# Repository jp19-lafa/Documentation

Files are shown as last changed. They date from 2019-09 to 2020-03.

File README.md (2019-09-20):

[][contributors-url]
[][forks-url]
[][stars-url]
[][issues-url]
[][license-url]

<!-- PROJECT LOGO -->
<br />
<p align="center">
  <a href="https://github.com/jp19-lafa/Documentation">
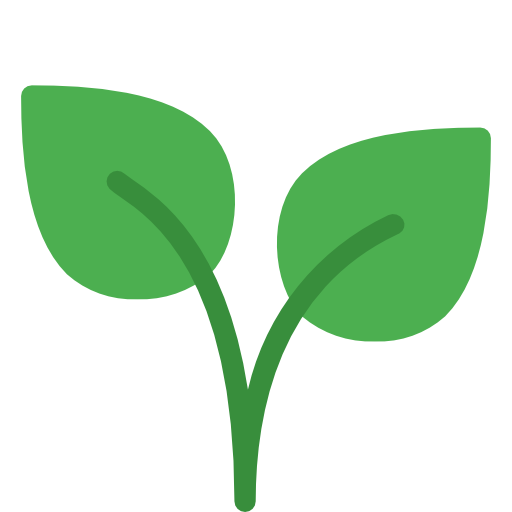
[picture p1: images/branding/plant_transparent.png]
    
  </a>

  <h3 align="center">DOCUMENTATION</h3>

  <p align="center">
    Wiki for farmlab
    <br />
    <a href="https://github.com/jp19-lafa/Documentation/wiki"><strong>Explore the docs »</strong></a>
    <br />
    <br />
    <a href="https://github.com/jp19-lafa/Documentation/issues">Report Bug</a>
    ·
    <a href="https://github.com/jp19-lafa/Documentation/issues">Request Feature</a>
  </p>
</p>

<!-- TABLE OF CONTENTS -->
## Table of Contents

* [Table of Contents](#table-of-contents)
* [About The Project](#about-the-project)
* [Roadmap](#roadmap)
* [Contributing](#contributing)
* [License](#license)
* [Team](#team)

<!-- ABOUT THE PROJECT -->
## About The Project
FarmLab is a class project for Smart Systems & IoT 2019 @ AP Antwerp. FarmLab is an automated hydroponics farm that utilizes an array of sensor to make smart decisions an create the optimal growing environment. Multiple nodes can work together to create a big farm network.

The cultivation of these plants follow the 'hydroponics' technique. This means the plants are planted directly in water without any type of soil. They are fed by nutrients added to that water.

_For the full explination please refer to the [Wiki](https://github.com/jp19-lafa/Documentation/wiki)_

<!-- ROADMAP -->
## Roadmap

See the [open issues](https://github.com/jp19-lafa/Documentation/issues) for a list of proposed features (and known issues).

<!-- CONTRIBUTING -->
## Contributing

Contributions are what make the open source community such an amazing place to be learn, inspire, and create. Any contributions you make are **greatly appreciated**.

1. Fork the Project
2. Create your Feature Branch (`git checkout -b feature/AmazingFeature`)
3. Commit your Changes (`git commit -m 'Add some AmazingFeature'`)
4. Push to the Branch (`git push origin feature/AmazingFeature`)
5. Open a Pull Request

<!-- LICENSE -->
## License

Distributed under the MIT License. See `LICENSE` for more information.

<!-- Team -->
## Team

Meurs Michiel - michiel.meurs1@gmail.com
<br>
Meyers Tom - tom@odex.be
<br>
Van Hoof Jonas - Jonas.vanhoof@student.ap.be
<br>
Vinck Ben - <!-- TODO: add a e-mail of Vincks choosing-->
<br>
Willemsen Matthias - <!-- TODO: add a e-mail of Willemsen's choosing-->

Project Link: [https://github.com/jp19-lafa/Documentation](https://github.com/jp19-lafa/Documentation)

<!-- MARKDOWN LINKS & IMAGES -->
<!-- https://www.markdownguide.org/basic-syntax/#reference-style-links -->
[contributors-shield]: https://img.shields.io/github/contributors/jp19-lafa/Documentation.svg?style=flat-square
[contributors-url]: https://github.com/jp19-lafa/Documentation/graphs/contributors
[forks-shield]: https://img.shields.io/github/forks/jp19-lafa/Documentation.svg?style=flat-square
[forks-url]: https://github.com/jp19-lafa/Documentation/network/members
[stars-shield]: https://img.shields.io/github/stars/jp19-lafa/Documentation.svg?style=flat-square
[stars-url]: https://github.com/jp19-lafa/Documentation/stargazers
[issues-shield]: https://img.shields.io/github/issues/jp19-lafa/Documentation.svg?style=flat-square
[issues-url]: https://github.com/jp19-lafa/Documentation/issues
[license-shield]: https://img.shields.io/github/license/jp19-lafa/Documentation.svg?style=flat-square
[license-url]: https://github.com/jp19-lafa/Documentation/blob/master/LICENSE.txt
[product-screenshot]: https://raw.githubusercontent.com/jp19-lafa/Documentation/master/images/branding/plant_transparent.svg

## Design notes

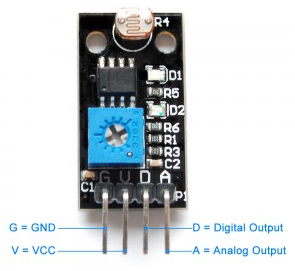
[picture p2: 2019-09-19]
images/sensors/Pinout_LightSensor.png

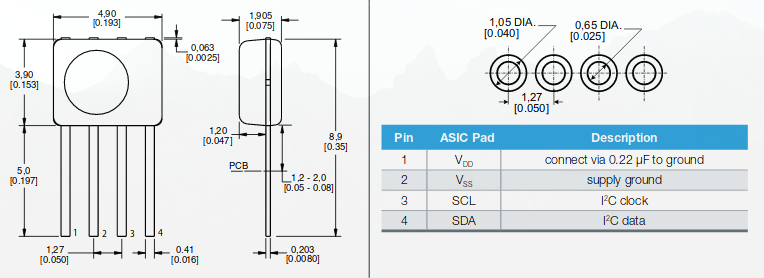
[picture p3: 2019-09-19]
images/sensors/Pinout_HIH6030.png

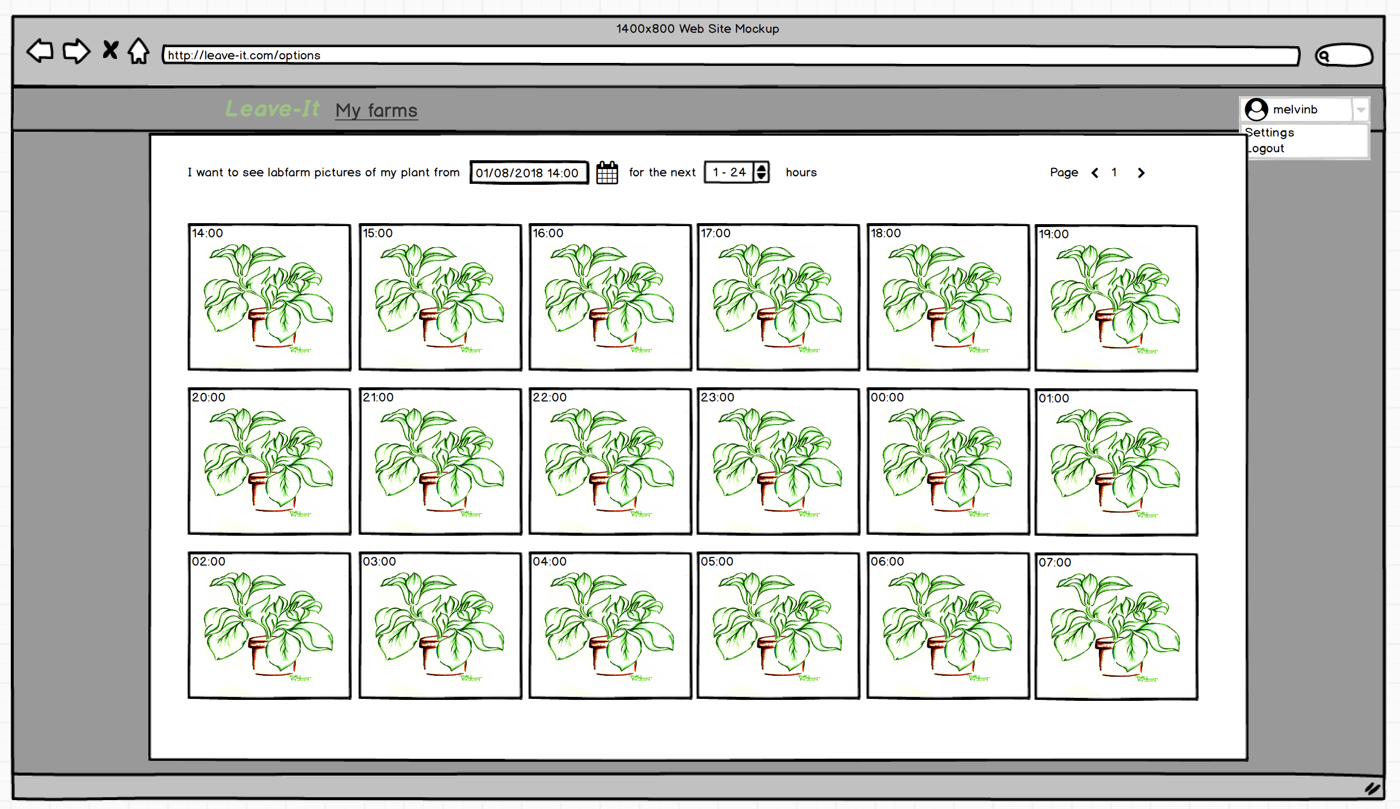
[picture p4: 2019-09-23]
images/web/labfarm_picture_overview_mockup.png

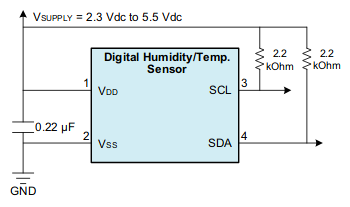
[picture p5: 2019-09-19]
images/sensors/Schematic_HIHI6030.png

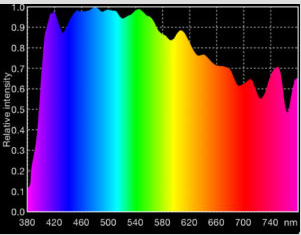
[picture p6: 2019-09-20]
images/actuators/Light_spectrum.png

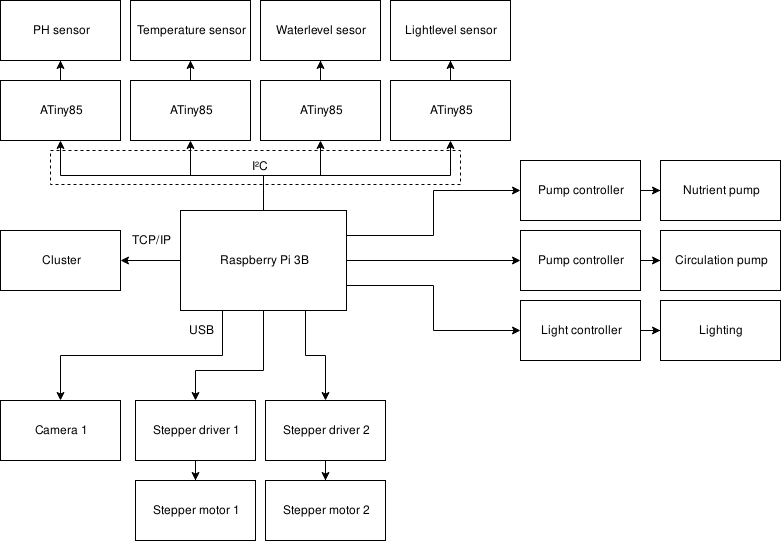
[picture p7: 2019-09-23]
images/general/hardware_blockdiagram.png

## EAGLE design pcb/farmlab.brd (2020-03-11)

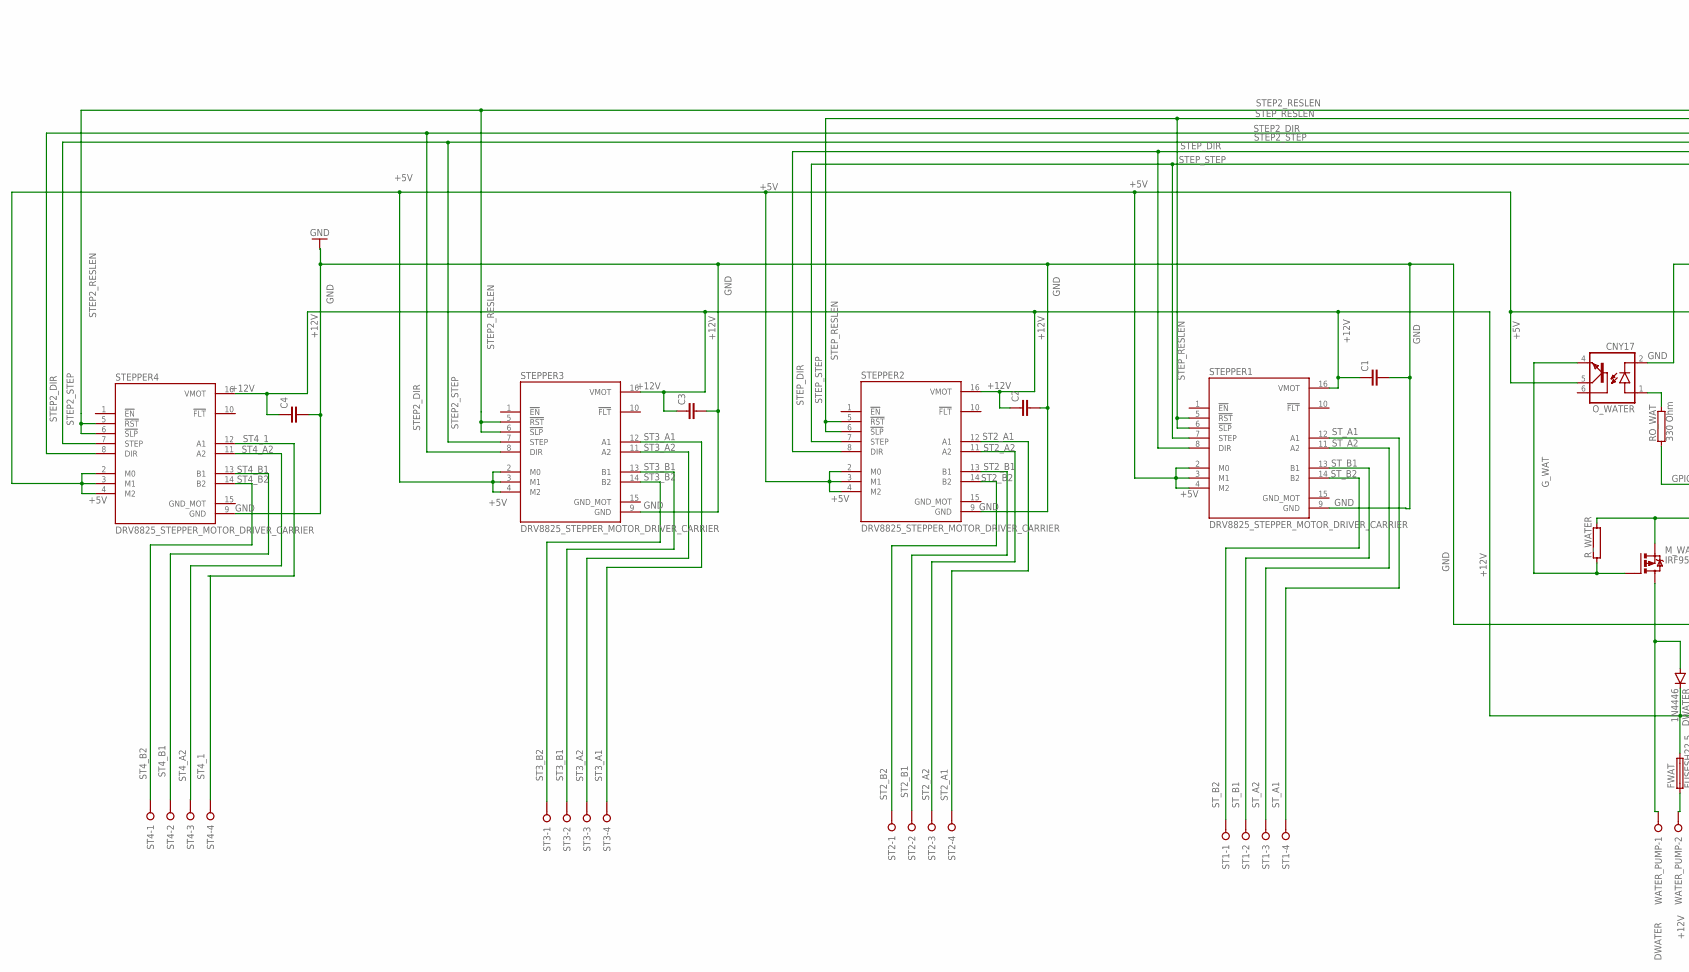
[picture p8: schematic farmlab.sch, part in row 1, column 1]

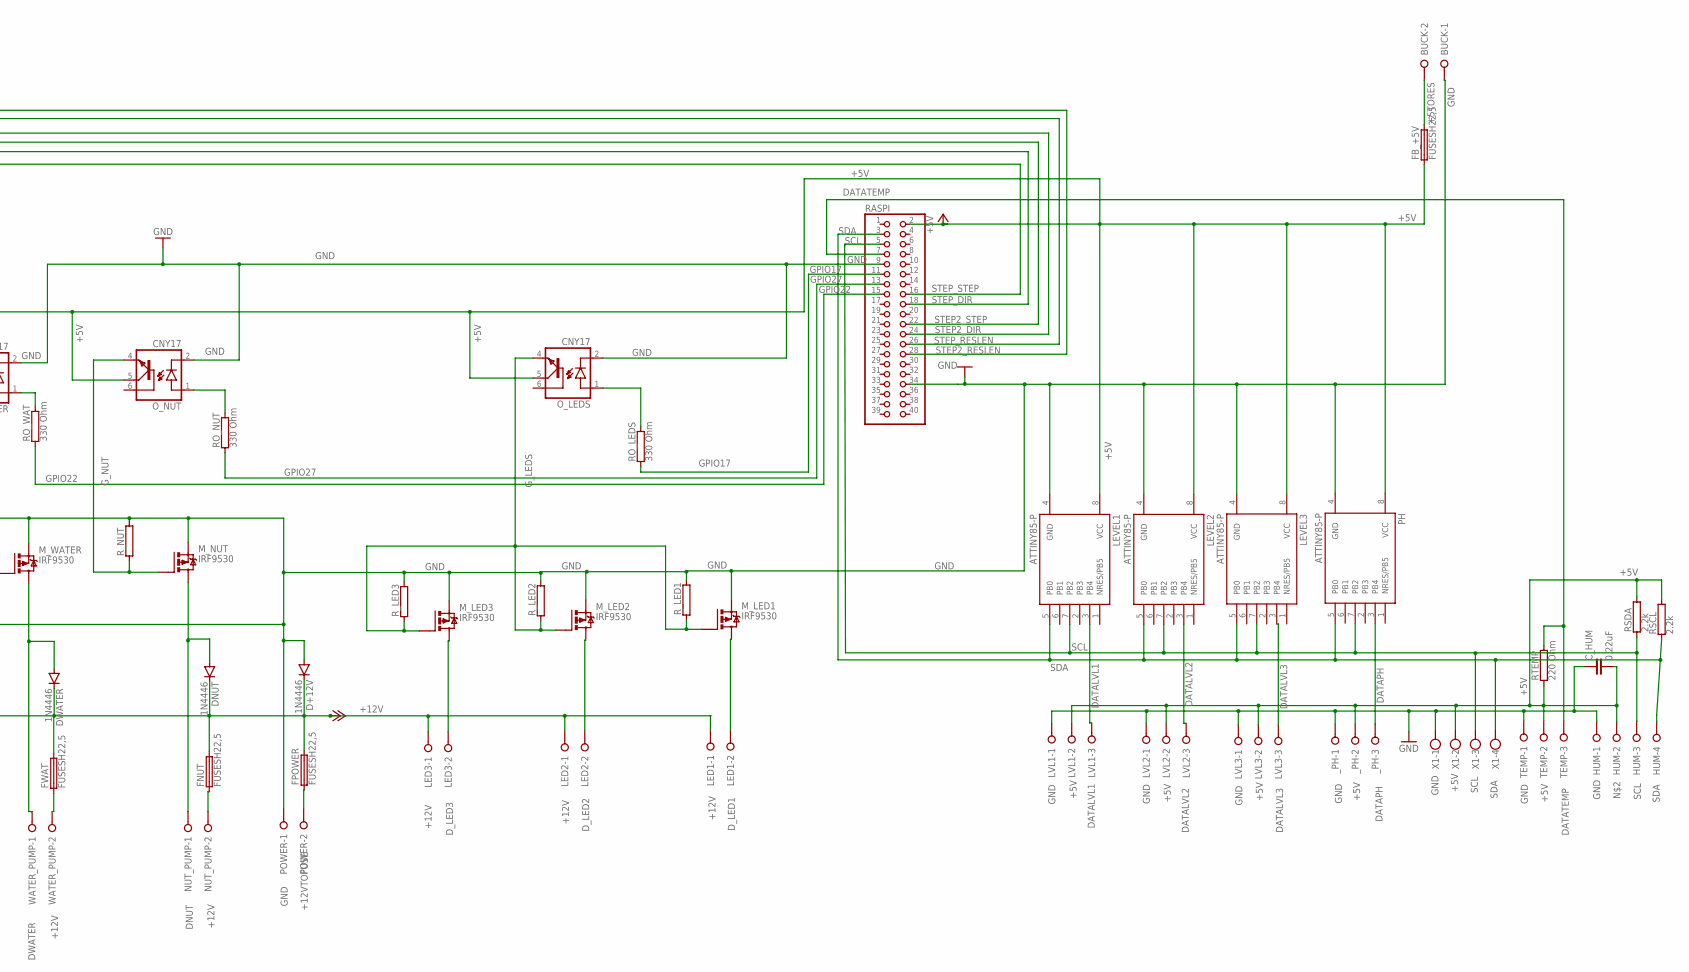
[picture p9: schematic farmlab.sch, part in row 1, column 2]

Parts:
BUCK: W237-02P; W237-132
C1, C2, C3, C4: C2.5/6; C2.5-6
C_HUM: 0.22uF; C2.5-6
D+12V: 1N4446; DO35-10
DNUT: 1N4446; DO35-10
DWATER: 1N4446; DO35-10
FB_+5V: FUSESH22,5; SH22,5
FNUT: FUSESH22,5; SH22,5
FPOWER: FUSESH22,5; SH22,5
FWAT: FUSESH22,5; SH22,5
HUM: W237-04P; W237-4P
LED1, LED2, LED3: W237-02P; W237-132
LEVEL1, LEVEL2, LEVEL3: ATTINY85-P; PDIP08_300MIL
LVL1, LVL2, LVL3: W237-3E
M_LED1, M_LED2, M_LED3: IRF9530; TO220BV
M_NUT: IRF9530; TO220BV
M_WATER: IRF9530; TO220BV
NUT_PUMP: W237-02P; W237-132
O_LEDS: CNY17; DIL06
O_NUT: CNY17; DIL06
O_WATER: CNY17; DIL06
PH: ATTINY85-P; PDIP08_300MIL
POWER: W237-02P; W237-132
RASPI: PINHD-2X20; 2X20
RO_LEDS: 330 Ohm; AC03
RO_NUT: 330 Ohm; AC03
RO_WAT: 330 Ohm; AC03
RSCL: 2.2k; AC03
RSDA: 2.2k; AC03
RTEMP: 220 Ohm; AC03
R_LED1, R_LED2, R_LED3: RAC03; AC03
R_NUT: RAC03; AC03
R_WATER: RAC03; AC03
ST1, ST2, ST3, ST4: W237-04P; W237-4P
STEPPER1, STEPPER2, STEPPER3, STEPPER4: DRV8825_STEPPER_MOTOR_DRIVER_CARRIER; IC_DRV8825_STEPPER_MOTOR_DRIVER_CARRIER
TEMP: W237-3E
WATER_PUMP: W237-02P; W237-132
X1: W237-4
_PH: W237-3E

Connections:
+5TORES: BUCK.2, FB_+5V.2
+5V: C_HUM.2, FB_+5V.1, LEVEL1.8 (VCC), LEVEL2.8 (VCC), LEVEL3.8 (VCC), LVL1.2, LVL2.2, LVL3.2, O_LEDS.5 (COL), O_NUT.5 (COL), O_WATER.5 (COL), PH.8 (VCC), RASPI.2, RSCL.2, RSDA.2, RTEMP.1, STEPPER1.2 (M0), STEPPER1.3 (M1), STEPPER1.4 (M2), STEPPER2.2 (M0), STEPPER2.3 (M1), STEPPER2.4 (M2), STEPPER3.2 (M0), STEPPER3.3 (M1), STEPPER3.4 (M2), STEPPER4.2 (M0), STEPPER4.3 (M1), STEPPER4.4 (M2), TEMP.2, X1.2, _PH.2
+12V: C1.1, C2.1, C3.1, C4.1, D+12V.C, DNUT.C, DWATER.C, FNUT.2, FPOWER.2, FWAT.2, LED1.1, LED2.1, LED3.1, STEPPER1.16 (VMOT), STEPPER2.16 (VMOT), STEPPER3.16 (VMOT), STEPPER4.16 (VMOT)
+12VTOFUSE: FPOWER.1, POWER.2
DATALVL1: LEVEL1.3 (PB4), LVL1.3
DATALVL2: LEVEL2.3 (PB4), LVL2.3
DATALVL3: LEVEL3.3 (PB4), LVL3.3
DATAPH: PH.3 (PB4), _PH.3
DATATEMP: RASPI.7, RTEMP.2, TEMP.3
DNUT: DNUT.A, M_NUT.D, NUT_PUMP.1
DWATER: DWATER.A, M_WATER.D, WATER_PUMP.1
D_LED1: LED1.2, M_LED1.D
D_LED2: LED2.2, M_LED2.D
D_LED3: LED3.2, M_LED3.D
GND: BUCK.1, C1.2, C2.2, C3.2, C4.2, C_HUM.1, D+12V.A, HUM.1, LEVEL1.4 (GND), LEVEL2.4 (GND), LEVEL3.4 (GND), LVL1.1, LVL2.1, LVL3.1, M_LED1.S, M_LED2.S, M_LED3.S, M_NUT.S, M_WATER.S, O_LEDS.2 (C), O_NUT.2 (C), O_WATER.2 (C), PH.4 (GND), POWER.1, RASPI.9, RASPI.34, R_LED1.2, R_LED2.2, R_LED3.2, R_NUT.2, R_WATER.2, STEPPER1.9 (GND), STEPPER2.9 (GND), STEPPER3.9 (GND), STEPPER4.9 (GND), TEMP.1, X1.1, _PH.1
GND_MOT: STEPPER1.15 (GND_MOT), STEPPER2.15 (GND_MOT), STEPPER3.15 (GND_MOT), STEPPER4.15 (GND_MOT)
GPIO17: RASPI.11, RO_LEDS.1
GPIO22: RASPI.15, RO_WAT.1
GPIO27: RASPI.13, RO_NUT.1
G_LEDS: M_LED1.G, M_LED2.G, M_LED3.G, O_LEDS.4 (EMI), R_LED1.1, R_LED2.1, R_LED3.1
G_NUT: M_NUT.G, O_NUT.4 (EMI), R_NUT.1
G_WAT: M_WATER.G, O_WATER.4 (EMI), R_WATER.1
unnamed: O_WATER.1 (A), RO_WAT.2
unnamed: O_NUT.1 (A), RO_NUT.2
unnamed: O_LEDS.1 (A), RO_LEDS.2
unnamed: FNUT.1, NUT_PUMP.2
unnamed: FWAT.1, WATER_PUMP.2
SCL: HUM.3, LEVEL1.7 (PB2), LEVEL2.7 (PB2), LEVEL3.7 (PB2), PH.7 (PB2), RASPI.5, RSDA.1, X1.3
SDA: HUM.4, LEVEL1.5 (PB0), LEVEL2.5 (PB0), LEVEL3.5 (PB0), PH.5 (PB0), RASPI.3, RSCL.1, X1.4
ST2_A1: ST2.4, STEPPER2.12 (A1)
ST2_A2: ST2.3, STEPPER2.11 (A2)
ST2_B1: ST2.2, STEPPER2.13 (B1)
ST2_B2: ST2.1, STEPPER2.14 (B2)
ST3_A1: ST3.4, STEPPER3.12 (A1)
ST3_A2: ST3.3, STEPPER3.11 (A2)
ST3_B1: ST3.2, STEPPER3.13 (B1)
ST3_B2: ST3.1, STEPPER3.14 (B2)
ST4_1: ST4.4, STEPPER4.12 (A1)
ST4_A2: ST4.3, STEPPER4.11 (A2)
ST4_B1: ST4.2, STEPPER4.13 (B1)
ST4_B2: ST4.1, STEPPER4.14 (B2)
STEP2_DIR: RASPI.24, STEPPER3.8 (DIR), STEPPER4.8 (DIR)
STEP2_RESLEN: RASPI.28, STEPPER3.5 (!RST), STEPPER3.6 (!SLP), STEPPER4.5 (!RST), STEPPER4.6 (!SLP)
STEP2_STEP: RASPI.22, STEPPER3.7 (STEP), STEPPER4.7 (STEP)
STEP_DIR: RASPI.18, STEPPER1.8 (DIR), STEPPER2.8 (DIR)
STEP_RESLEN: RASPI.26, STEPPER1.5 (!RST), STEPPER1.6 (!SLP), STEPPER2.5 (!RST), STEPPER2.6 (!SLP)
STEP_STEP: RASPI.16, STEPPER1.7 (STEP), STEPPER2.7 (STEP)
ST_A1: ST1.4, STEPPER1.12 (A1)
ST_A2: ST1.3, STEPPER1.11 (A2)
ST_B1: ST1.2, STEPPER1.13 (B1)
ST_B2: ST1.1, STEPPER1.14 (B2)

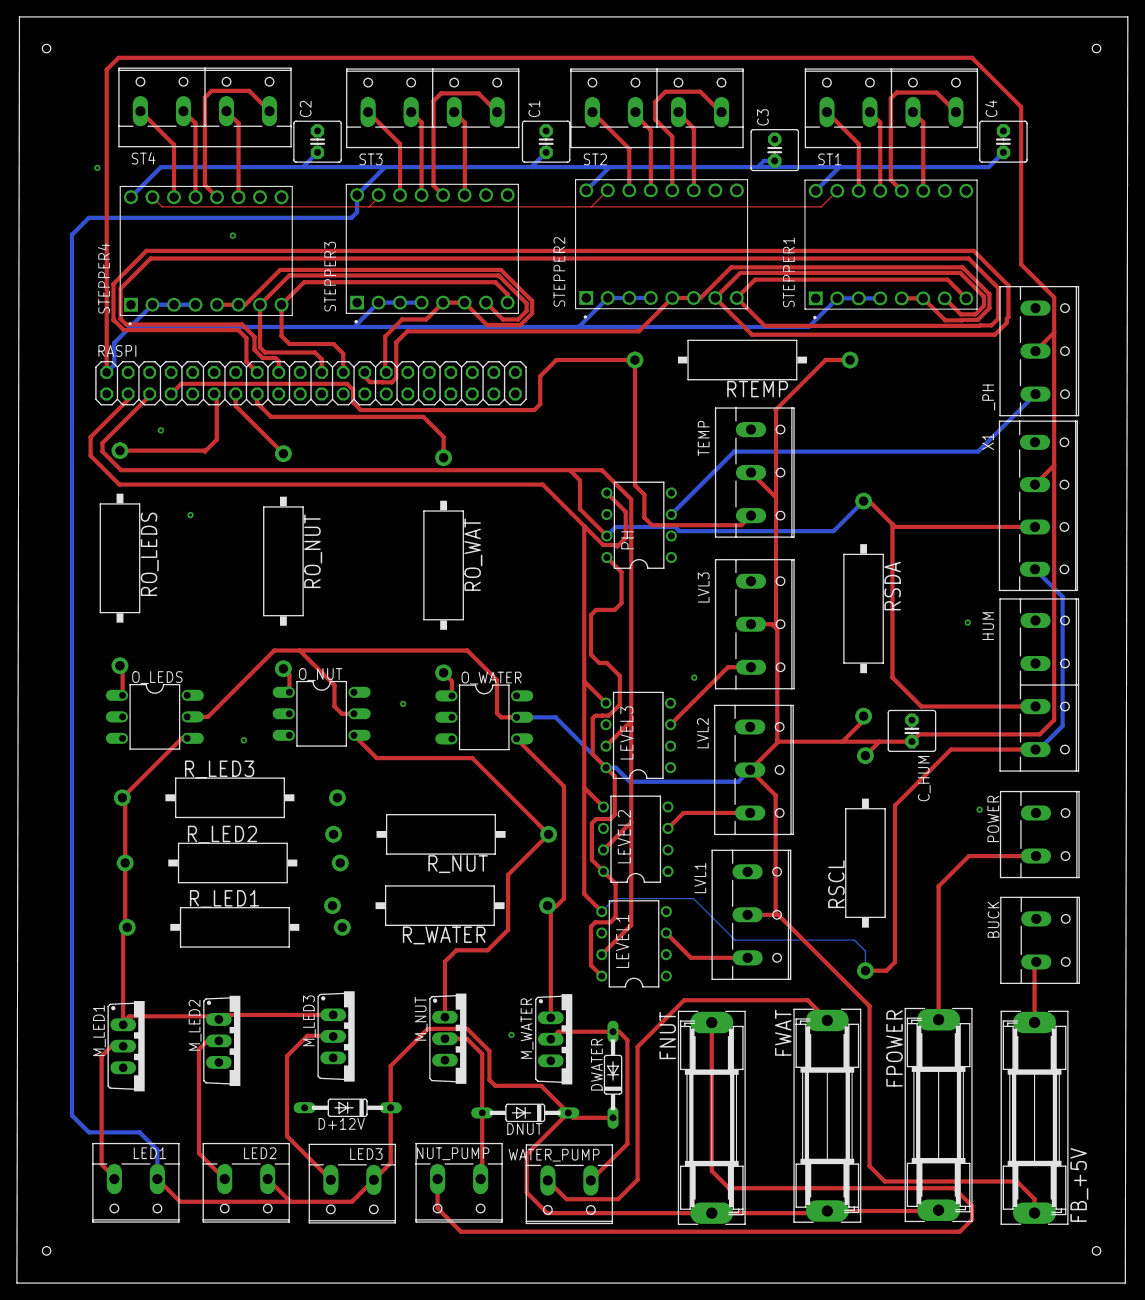
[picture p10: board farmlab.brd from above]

Board: 2 copper layers, 131.2 x 149.5 mm, 58 parts (0 on the bottom side), 51 nets.

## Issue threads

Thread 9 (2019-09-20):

[REFACTOR] readme email list

ShiftyMLG, 2019-09-20:
**Describe the current issue**
E-mails are still missing

**Where is the problem**
What piece of code is a problem
* file: README.md

**How should it change**
Add e-mails

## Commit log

2019-09-16 Added specifications of the sensors + images
2019-09-17 Moved images to Images/Branding All the images that I used in my document Sensors.md where moved to the path Images/Branding.
2019-09-17 Added coding rules to Sensors.md Corrected the style of the document to the coding ruls for a markdown document.
2019-09-19 Moved sensor images Added directory /images/sensors. Moved the sensor images from images/branding to /images/sensors.
2019-09-19 Updated Sensors.md Centered the sensor images and changed the image links. Added the level sensor analysis to the document.
2019-09-19 Deleted Sensors.md Added the content of Sensors.md to the wiki => Analysis => Sensors. Deleted Sensors.md to clean the work tree.
2019-09-19 [ImgBot] Optimize images
    *Total -- 147.66kb -> 99.32kb (32.73%)
    /images/sensors/Ph_scale.png -- 58.96kb -> 23.44kb (60.24%)
    /images/sensors/Schematic_HIHI6030.png -- 10.53kb -> 8.33kb (20.85%)
    /images/sensors/Pinout_HIH6030.png -- 73.60kb -> 63.47kb (13.76%)
    /images/sensors/Pinout_DS18B20.png -- 4.57kb -> 4.08kb (10.81%)
2019-09-20 Added images and actuator analysis.md Added a document that analyses all the actuators use in Farmlab. All images used in actuators.md are added in images/actuators.
2019-09-20 Updated actuators.md Added the stepper motor driver to the analysis.
2019-09-23 [ImgBot] Optimize images
    *Total -- 3,223.91kb -> 1,994.49kb (38.13%)
    /images/flowcharts/ATTiny_flowchart.png -- 44.20kb -> 13.96kb (68.41%)
    /images/general/hardware_blockdiagram.png -- 27.52kb -> 13.25kb (51.85%)
    /images/web/erd_database.png -- 98.04kb -> 48.95kb (50.07%)
    /images/web/node_unreliable.png -- 15.34kb -> 8.29kb (45.95%)
    /images/general/state_diagram.png -- 23.23kb -> 13.03kb (43.91%)
    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
2019-10-10 Added PCB relaed images Added in folder images/PCB/ Schematic.png and Board.png
2019-10-10 Added Manufactered PCB board image Changed folder name images/PCB to images/pcb. 3D model of the future PCB board added in images/pcb/
2019-10-11 [ImgBot] Optimize images
    *Total -- 143.30kb -> 101.90kb (28.89%)
    /images/pcb/Board.png -- 31.04kb -> 15.26kb (50.84%)
    /images/pcb/Schematic.png -- 16.80kb -> 9.44kb (43.8%)
    /images/pcb/Manufactered_Board.png -- 93.47kb -> 75.50kb (19.23%)
    /images/branding/plant_transparent.svg -- 1.99kb -> 1.70kb (14.17%)
2020-03-11 Added pcb scheme
    - added the most recent pcb schema from jp19-lafa
    [farmlab.brd, farmlab.sch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]
